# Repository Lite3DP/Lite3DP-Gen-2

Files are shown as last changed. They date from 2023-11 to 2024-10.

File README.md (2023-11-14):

# Lite3DP Gen 2

CAMP-8-pledge2a

Hi everyone! Thanks for stopping by here!

We are delighted to introduce the new Lite3DP Gen 2. We will be here expanding and improving the open source documentation, with a focus on the study, modification, improvement and repair of the kits and pre-assembled machines offered on [Crowd Supply](https://www.crowdsupply.com/lite3dp/lite3dp-gen-2).

Due to the need to introduce custom components and more complex manufacturing processes, we have moved slightly away from the strong DIY imprint of the S1 model, in which all the components are standard and the soldering with through-hole. However, for those enthusiasts who want to build an entirely Gen 2-style machine (OLED auxiliary display suggested), below we list non-standard components and possible adaptations/solutions.

1. SMD soldering.
Most electronic components are no longer through-hole and surface mount must be performed. It's not as simple as with a soldering iron, but you can order a stencil along with the PCBs, use solder paste and an electric oven or heat gun to achieve reflow. Please research this topic carefully.

2. Stepper motor.
We incorporate a custom stepper motor: Nema 8 with built-in T3.5 leadscrew, 128mm long. This is not a standard motor, but it is common to find a 100mm long leadscrew, which you can use only by giving up a few millimeters of build height.
   
3. LCD display.
We use a non-standard LCD display, with custom FPC cable and protective glass. You can get it as a spare part on [Crowd Supply](https://www.crowdsupply.com/lite3dp/lite3dp-gen-2).
   
4. Linear guide.
Like the stepper motor leadscrew, the 115mm length of the linear guide is not common, but you can also use 100mm length instead.
   
5. Aluminum light cone.
The original cone is made from aluminum, offering a large additional heat dissipation surface area. Use the plastic model with caution that the LCD display does not exceed 60°C. You can apply aluminum film inside and reduce the power of UV light.
    
6. Resin vat / build platform.
Resin vat can be made of plastic only in PLA and PP since other materials chemically react with resins. In the plastic alternative resin vat design, the Gerber of an aluminum PCB is included from which it can be cut out and obtain the vat frame and the surface of the build platform. This way it is not necessary to order metal cutting parts, and they can be ordered together with the PCBs.

Please visit our website [Lite3DP.com](https://www.lite3dp.com/) and we welcome inquiries at support@lite3dp.com. Thank you!

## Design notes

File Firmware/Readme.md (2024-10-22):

Please install ESP32 boards core **version 2.0.17** or earlier for Arduino IDE. (Newer 3.X.X versions have renamed some functions).

Attached "example.png" is an example section that, when copied to the root of the micro SD card, allows you to run the "Factory test".

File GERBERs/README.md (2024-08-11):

**Main board:**





**Aluminum base board:**



**OLED board:**



**4PDT switch board:**



**AUX CONN BOARD:**



**EXPANSION SHIELD (BETA):**



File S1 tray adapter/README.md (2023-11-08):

The S1 resin tray adapter can be printed on the S1 itself or on a filament 3D printer as well.
Please print two units, one for each side of the tray.

You will additionally need 4 M3x8 button head screws and 4 M3 nuts. (The magnets on the main board are not necessary. The resin tray attachment system is sliding, no longer magnetic).

Please note that the S1 build platform is perfectly compatible with the new Gen 2 Dev kit.



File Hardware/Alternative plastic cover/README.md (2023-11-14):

Plastic cover to be 3D printed.



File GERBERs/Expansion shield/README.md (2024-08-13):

**BETA version**

This is a 4 layer PCB, containing:

- 1 x Stepper motor driver (slow motion due to I2C conn.), with motor connector and microstep selector (1x3 dip switch).
- 2 x Servo outputs (+5V lvl).
- 2 x Endstops input (+5V lvl).
- 1 x +12V output (typ. a 12V fan).
- 1 x Buzzer.
- 5 x GPIO +3V3 lvl.
- 2 x GPIO +5V lvl.



You can use the following library for its control:

https://github.com/adafruit/Adafruit_AW9523?tab=readme-ov-file

To be plugged into the Gen 2 auxiliary connector.

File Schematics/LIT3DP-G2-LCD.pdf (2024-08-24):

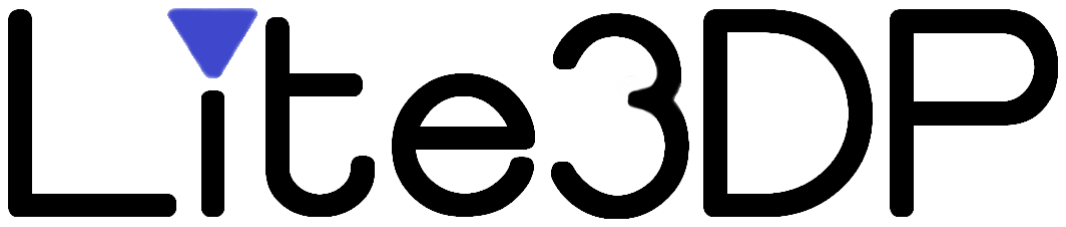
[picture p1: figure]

LITE3DP-G2-LCD | REV 1.0

# GEN 2

# SPECIFICATION FOR LCD MODULE

# LITE3DP-G2-LCD

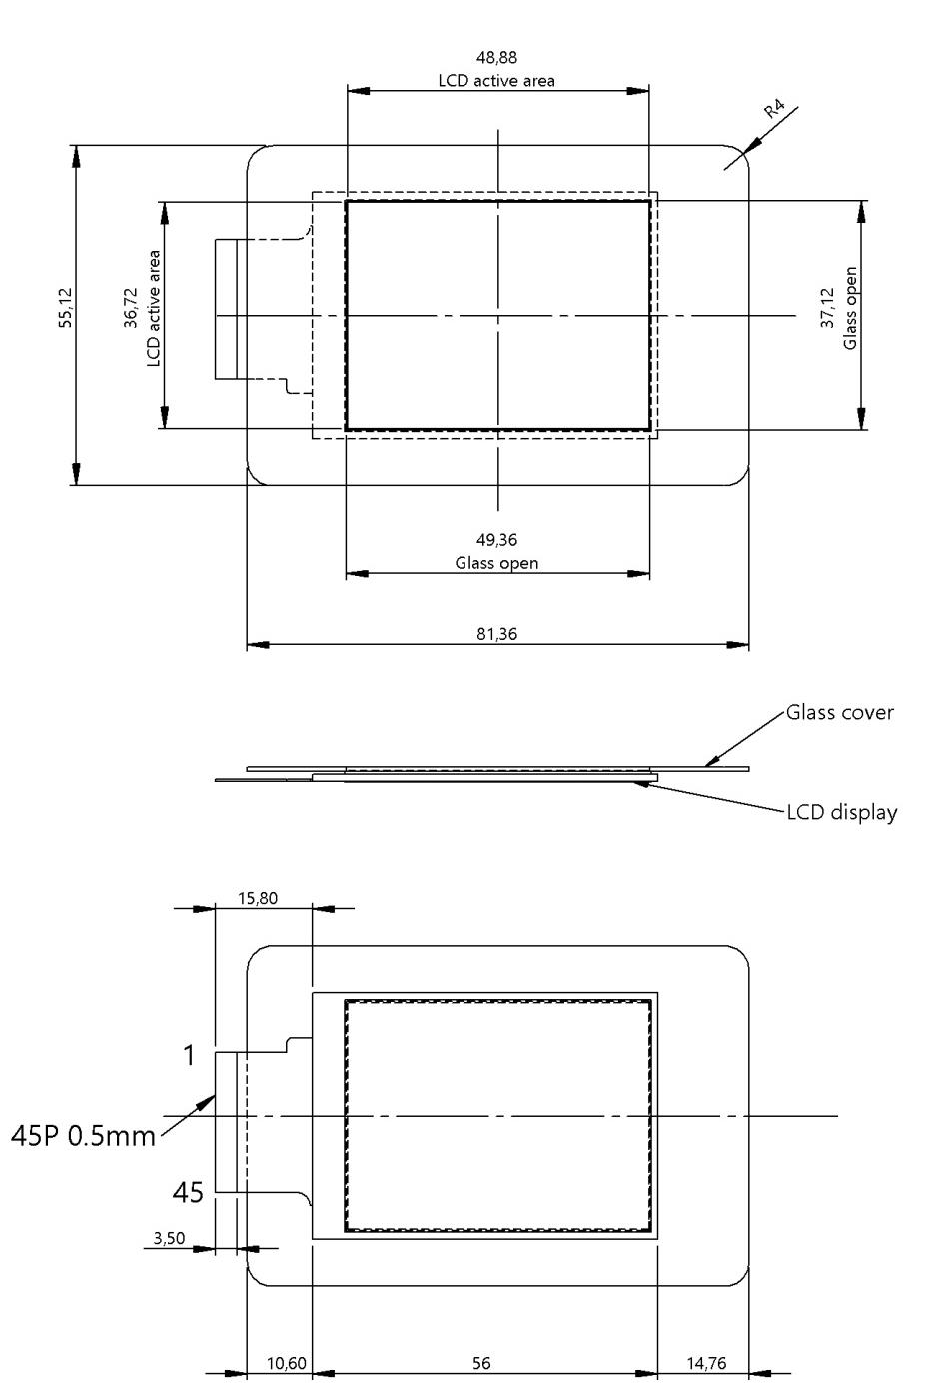
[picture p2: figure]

LITE3DP-G2-LCD | REV 1.0

PIN N°
1 | GND
2 | VCI
3 | IOVCC
4 | IM2
5 | IM1
6 | IM0
7 | RST
8 | CS
9 | DC
10 | WR(SPI SCL)
11 | RD
12 | VSYNC
13 | HSYNC
14 | ENABLE
15 | DOTCLK
16 | SDA
17 | DB0
18 | DB01
19 | DB02
20 | DB03
21 | DB04
22 | DB05
23 | DB06
24 | DB07
25 | DB08
26 | DB09
27 | DB10
28 | DB11
29 | DB12
30 | DB13
31 | DB14
32 | DB15
33 | DB16
34 | DB17
35 | SDO
36 | NC
37 | NC
38 | NC
39 | NC
40 | NC
41 | NC
42 | NC
43 | NC
44 | NC
45 | GND
DISPLAY TYPE | 2.4” – TFT LCD. 65K/262K COLORS
ACTIVE AREA | 36.72 x 48.88 mm
NUMBER OF PIXELS | 320(RGB) X 426
PIXEL PITCH | 0.11475 X 0.11475 mm
DISPLAY MODE | TRANSMISSIVE/NORMALLY BLACK
VIEWING DIRECTION | ALL
LCM DRIVER IC | ST7796S
LCM INTERFACE | SPI+RGB/MCU
VDD/VCI | 3.3V; IOVCC: 1.8-3.3V
OPERATING TEMPERATURE STORAGE TEMPERATURE | -20°C TO 70°C -30°C TO 80°C
ROHS COMPLIANT | YES

IM2 = IM1 = IM0 = 1: 4-WIRE 8 BIT DATA SERIAL INTERFACE (SDA, SCL, CS, RS).

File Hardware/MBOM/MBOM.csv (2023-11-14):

Nuts & screws | Qty
Aluminum spacers, length 35mm | 7
Nylon spacer, length 35mm | 1
M3x6 screw, allen button head | 10
M3x8 screw, allen button head | 24
M2x6 screw, allen cylindrical head | 8
M3x10 screw, allen countersunk head | 4
M3x10 hand knob screw | 1
M2x8 screw, allen cylindrical head | 3
M2 nuts | 4
M3 nuts | 4
Mechanical components
NEMA 8, leadscrew T3.5, length 118mm | 1
Linear guide rail MGN7, length 115 mm + MGN7C block | 1

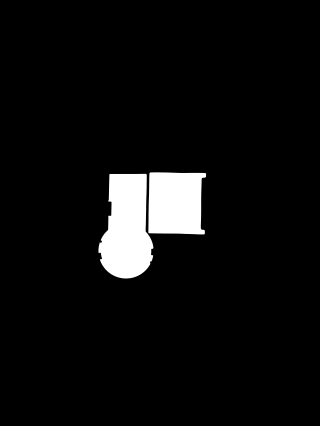
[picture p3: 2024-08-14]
Firmware/example.png

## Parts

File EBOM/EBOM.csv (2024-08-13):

 | MAIN BOARD
ID | Name | Designator | Footprint | Quantity | Manufacturer Part | Manufacturer | Supplier | Supplier Part
1 | 100nF | C2,C6,C8 | C0805 | 3 | GRM21BR71H104KA01L | MuRata | LCSC | C77082
2 | 10uF | C3 | C0805 | 1 | 0805X106K250NT | FH | LCSC | C40894
3 | 22uF | C7 | C0805 | 1 | CL21A226MAYNNNE | Samsung Electro-Mechanics | LCSC | C602037
4 | SS34_C8678 | D2 | DO-214AC_L4.3-W2.7-LS5.3-RD | 1 | SS34 | MDD | LCSC | C8678
5 | FH-00538 | H2 | HDR-SMD_12P-P2.54-V-F-R2-C6-S7.0-EH | 1 | FH-00538 | Liansheng(??) | LCSC | C2685123
6 | 150? | R3,R18 | R0805 | 2 | 0805W8J0151T5E | UniOhm | LCSC | C25283
7 | 10k? | R4,R5,R6,R7,R8,R9,R10,R11,R12,R19 | R0805 | 10 | RTT05103JTP | RALEC | LCSC | C103914
8 | 100k? | R13,R14,R15 | R0805 | 3 | RTT05104JTP | RALEC | LCSC | C103915
9 | 5.1k? | R16 | R0805 | 1 | 0805W8J0512T5E | UniOhm | LCSC | C26023
10 | ESP32-WROOM-32E(4MB) | U5 | WIFI-SMD_ESP32-WROOM-32E | 1 | ESP32-WROOM-32E(4MB) | Espressif Systems | LCSC | C701341
11 | DSHP03TS-S | SW1 | SW-SMD_DSHP03TS-S | 1 | DSHP03TS-S | XKB Enterprise | LCSC | C319051
12 | GT-TC029B-H025-L1N | BOOT,RST | SW-SMD_L3.9-W2.9-P4.15-LS5.0 | 2 | GT-TC029B-H025-L1N | G-Switch | LCSC | C843669
13 | 19-217/G7C-AN1P2/3T | LED1 | LED0603-R-RD | 1 | 19-217/G7C-AN1P2/3T | EVERLIGHT | LCSC | C72042
14 | PT4115 | U1 | SOT-89-5_L4.5-W2.5-P1.50-LS4.5-BR | 1 | PT4115 | UMW(???????) | LCSC | C347356
15 | LR1117DS33X | U2 | SOT-223_L6.3-W3.5-P2.30-LS7.0-BR-1 | 1 | LR1117DS33X | Leshan Radio | LCSC | C383259
16 | 100uF | C1 | SMD,D6.3xL7.7mm | 1 | RVT1H101M0607 | ROQANG(??) | LCSC | C3151829
17 | 10uF | C4,C5 | CAP-SMD_L3.5-W2.8-R-RD | 2 | TAJB106M025RNJ | AVX | LCSC | C8018
18 | TF-013 | CARD1 | TF-SMD_TF-013 | 1 | TF-013 | ???? | LCSC | C961683
19 | WAFER-254L-4P | CN2,CN4 | CONN-SMD_WAFER-254L-4P | 2 | WAFER-254L-4P | XUNPU(??) | LCSC | C2856686
20 | SS14_C211769 | D1 | SMA_L4.4-W2.8-LS5.4-RD | 1 | SS14 | Yangzhou Yangjie Elec Tech | LCSC | C211769
21 | THD0515-45CL-SN | FPC1 | FFC-SMD_45P-P0.50_THD0515-45CL-SN | 1 | THD0515-45CL-SN | THD | LCSC | C283158
22 | 47uH | L1 | IND-SMD_L5.0-W5.0_NR5040T | 1 | SNR5040TYD470M | SOREDE(???) | LCSC | C2827400
23 | D882 | Q1 | SOT-89-3_L4.5-W2.5-P1.50-LS4.2-BR | 1 | D882 | Hottech | LCSC | C181187
24 | 160m? | R1 | R2010 (1%) | 1 | RTT20R160FTE | RALEC | LCSC | C333477
25 | 180m? | R2 | R2010 (1%) | 1 | FRL2010FR180TS | FOJAN | LCSC | C2934352
26 | 30? | R17 | R2010 | 1 | RTT2030R0FTE | RALEC | LCSC | C458673
27 | SMD1206B075TF/16 | U8 | R1206 | 1 | SMD1206B075TF/16 | Brightking Elec (TAIWAN) | LCSC | C269118
28 | GT-TC041B-H036-L1N COPY | SP | G-SWITCH GT-TC041B-H036-L1N | 1 | GT-TC041B-H036-L1N | G-Switch(??) | LCSC | C2686893
29 | 2171-104MS0CUNR1 | U3 | CONN-SMD_2171-104MS0CUNR1 | 1 | 2171-104MS0CUNR1 | Wcon(????) | LCSC | C920937
30 | DC-050-20A | DC1 | DC-IN-SMD_DC-050-20A | 1 | DC-050-20A | ???? | LCSC | C707276
31 | F0502-B-12-20T-R | FPC2 | FPC-SMD_F0502-B-12-20T-R | 1 | F0502-B-12-20T-R | XFCN | LCSC | C705230
32 | DY-ITR8402 | U6 | OPTO-TH_DY-ITR8402 | 1 | DY-ITR8402 | TONYU | LCSC | C390039
33 | SS-12D10L4 | SW2 | SW-TH_SS-12D10L3 | 1 | SS-12D10L4 | XKB Connectivity | LCSC | C843364
34 | 2171-104MS0CUNR1 | U10, U11 | CONN-SMD_2171-108MS0CUNR1 | 2 | 2171-108MS0CUNR1 | Wcon(????)
35 | Custom LCD | - | LCD-display | 1 | LITE3DP-G2-LCD | LITE3DP |  |  | https://www.crowdsupply.com/lite3dp/lite3dp-gen-2
 | BASE BOARD
ID | Name | Designator | Footprint | Quantity | Manufacturer Part | Manufacturer | Supplier | Supplier Part
1 | LED-SMD_L3.5-W2.8-RD_1.25T-2PWT | U1,U2 | LED-SMD_L3.5-W2.8-RD_1.25T-2PWT | 2 | XL-2835UWC-02 | XINGLIGHT(???) | LCSC | C2843876
2 | WAFER-254L-4P | CN1 | CONN-SMD_WAFER-254L-4P | 1 | WAFER-254L-4P | XUNPU(??) | LCSC | C2856686
2 | LED 10W UV 405 nm | U3 | 6565 | 1 |  | YM | N/A on LCSC |  | https://aliexpress.com/item/1005004873818397.html
 |  |  |  |  |  |  |  |  | REMOVE QUARTZ LENS
 | OLED BOARD
ID | Name | Designator | Footprint | Quantity | Manufacturer Part | Manufacturer | Supplier | Supplier Part
1 | 10uF | C1,C3,C4,C5 | C0805 | 4 | 0805X106K250NT | FH | LCSC | C40894
2 | 100nF | C2 | C0805 | 1 | GRM21BR71H104KA01L | MuRata | LCSC | C77082
3 | 1125-1104G0Z135CR01 | CN1 | CONN-SMD_1125-1104G0Z135CR01 | 1 | 1125-1104G0Z135CR01 | Wcon(????) | LCSC | C721862
4 | LMBR120FT1G | D2 | SOD-123_L2.8-W1.8-LS3.7-RD | 1 | LMBR120FT1G | LRC(?????) | LCSC | C81143
5 | 10uH | L1 | L0805 | 1 | MGFL2012F100MT-LF | microgate | LCSC | C281113
6 | 12k? | R1,R3,R4 | R0805 | 3 | 0805W8J0123T5E | UniOhm | LCSC | C25616
7 | 100k? | R2 | R0805 | 1 | RTT05104JTP | RALEC | LCSC | C103915
8 | 680k? | R5 | R0805 | 1 | 0805W8J0684T5E | UniOhm | LCSC | C25640
9 | 2.2k? | R6,R7 | R0805 | 2 | CR0805J80222G | LIZ | LCSC | C101970
10 | AP3012KTR-G1 | U1 | SOT-23-5_L2.9-W1.6-P0.95-LS2.8-BL | 1 | AP3012KTR-G1 | DIODES(??) | LCSC | C102618
11 | APX803S-26SA-7 | U2 | SOT-23-3_L2.9-W1.6-P1.90-LS2.8-BR | 1 | APX803S-26SA-7 | DIODES(??) | LCSC | C526393
12 | OLED DISPLAY | ER-OLED0.96-7 | 13 pins | 1 | ER-OLED0.96-7 | EastRising | EastRising | ER-OLED0.96-7 | https://www.buydisplay.com/white-0-96-inch-64x128-oled-display-screen-sh1107-spi-i2c-interface
 | 4PDT SWITCH BOARD
ID | Name | Designator | Footprint | Quantity | Manufacturer Part | Manufacturer | Supplier | Supplier Part
1 |  | IN1, IN2, OUT1, OUT2 | Male Header, 4 Pins x 1 Row, Straight, P=2.54 mm | 4 | 210-91-04GB01 | PINREX | LCSC | C390680
2 | 4PDT SWITCH |  |  | 1 | T-80 |  |  |  | https://aliexpress.com/i/1005004254583326.html
 |  |  |  |  |  |  |  |  | ON OFF ON
 | AUX CONN BOARD
ID | Name | Designator | Footprint | Quantity | Manufacturer Part | Manufacturer | Supplier | Supplier Part
1 | X6511FRS-05-C85D30 | H1 | HDR-SMD_5P-P2.54-H-F_X6511FRS-19-C85D30 | 1 | X6511FRS-05-C85D30 | XKB Connectivity(????) | LCSC | C5142238
2 | PZ254V-12-12P | H2 | HDR-TH_12P-P2.54-V-M-R2-C6-S2.54 | 1 | PZ254V-12-12P | XFCN(??) | LCSC | C492423
3 | PM254V-12-12-H85 | H3 | HDR-TH_12P-P2.54-V-F-R2-C6-S2.54 | 1 | PM254V-12-12-H85 | XFCN(??) | LCSC | C541855
 | EXPANSION SHIELD
ID | Name | Designator | Footprint | Quantity | Manufacturer Part | Manufacturer | Supplier | Supplier Part
1 | Header-Female-2.54_1x8 | EN,VMOT | HDR-TH_8P-P2.54-V-F-1 | 2 | 2.54-1*8P??? | BOOMELE(????) | LCSC | C27438
2 | PZ254V-11-04P_C2691448 | MOT | HDR-TH_4P-P2.54-V-M | 1 | PZ254V-11-04P | XFCN(??) | LCSC | C2691448
3 | PZ254V-11-02P | H4,H2,FAN | HDR-TH_2P-P2.54-V-M | 3 | PZ254V-11-02P | XFCN(??) | LCSC | C492401
4 | TXS0108EPWR | U2 | TSSOP-20_L6.5-W4.4-P0.65-LS6.4-BL | 1 | TXS0108EPWR | TI(????) | LCSC | C17206
5 | 5.1K | R2,R5 | R0603 | 2 | RC0603JR-075K1L | YAGEO(??) | LCSC | C14677
6 | 10k? | R4,R3,R8,R6,R7 | R0603 | 5 | 0603WAJ0103T5E | UNI-ROYAL(??) | LCSC | C15401
7 | D882 | Q2,Q1 | SOT-89-3_L4.5-W2.5-P1.50-LS4.2-BR | 2 | D882 | Hottech | LCSC | C181187
8 | AMS1117-5.0_C347223 | U3 | SOT-223_L6.7-W3.5-P2.30-BR | 1 | AMS1117-5.0 | UMW(???????) | LCSC | C347223
9 | AW9523BTQR | U1 | VFQFPN-24_L4.0-W4.0-P0.50-BL-EP2.8 | 1 | AW9523BTQR | AWINIC(??) | LCSC | C148077
10 | SS34_C8678 | D2 | DO-214AC_L4.3-W2.7-LS5.3-RD | 1 | SS34 | MDD | LCSC | C8678
11 | 10uF | C5,C4 | CAP-SMD_L3.5-W2.8-R-RD | 2 | TAJB106M025RNJ | AVX | LCSC | C8018
12 | 100k? | R1 | R0603 | 1 | 0603WAJ0104T5E | UNI-ROYAL(??) | LCSC | C15458
13 | Header-Male-2.54_1x3 | E1,E2,S1,S2 | HDR-TH_3P-P2.54-V-M-1 | 4 | 2.54-1*3P? | BOOMELE(????) | LCSC | C49257
14 | MLT-5020 | BUZZ1 | BUZ-SMD_L5.0-W5.5-P4.60 | 1 | MLT-5020 | ?? | LCSC | C94598
15 | PZ254-1-13-Z-8.5 | H1 | HDR-TH_13P-P2.54-V-M | 1 | PZ254-1-13-Z-8.5 | HCTL(????) | LCSC | C2894936
16 | DSHP03TS-S | SW1 | SW-SMD_DSHP03TS-S | 1 | DSHP03TS-S | XKB Enterprise | LCSC | C319051
17 | 100uF | C1 | SMD,D6.3xL7.7mm | 1 | RVT1H101M0607 | ROQANG(??) | LCSC | C3151829
18 | 100nF | C2,C3 | C0603 | 2 | 0603B104K500NT | FH(??) | LCSC | C30926
19 | PZ254V-12-12P | H3 | HDR-TH_12P-P2.54-V-M-R2-C6-S2.54 | 1 | PZ254V-12-12P | XFCN(??) | LCSC | C492423

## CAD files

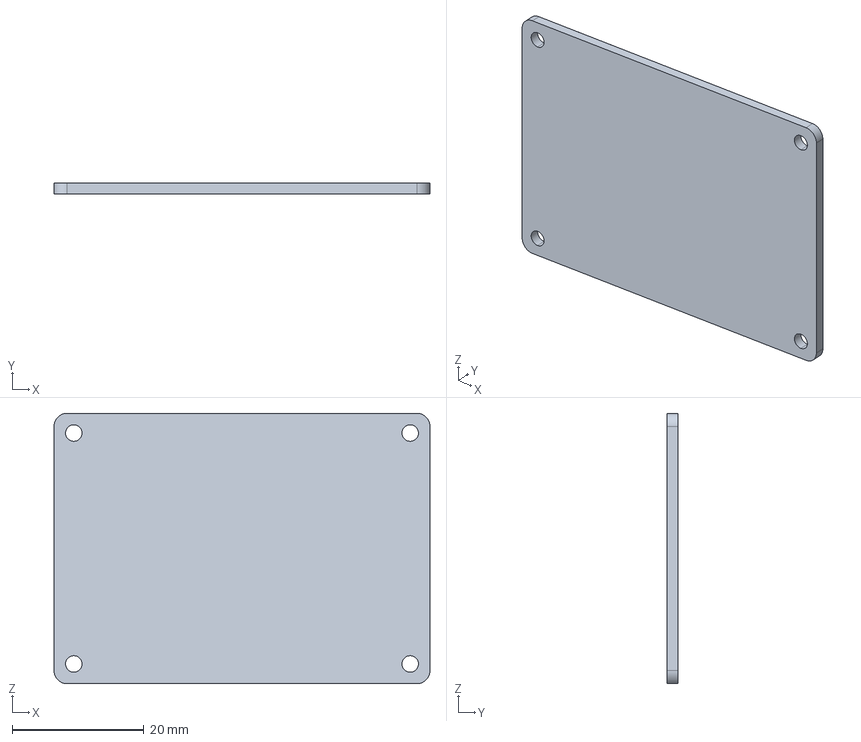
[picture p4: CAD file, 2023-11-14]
Alternative resin vat and build platform/Platform aluminum surface.STEP
57.0 x 1.60 x 41.0 mm

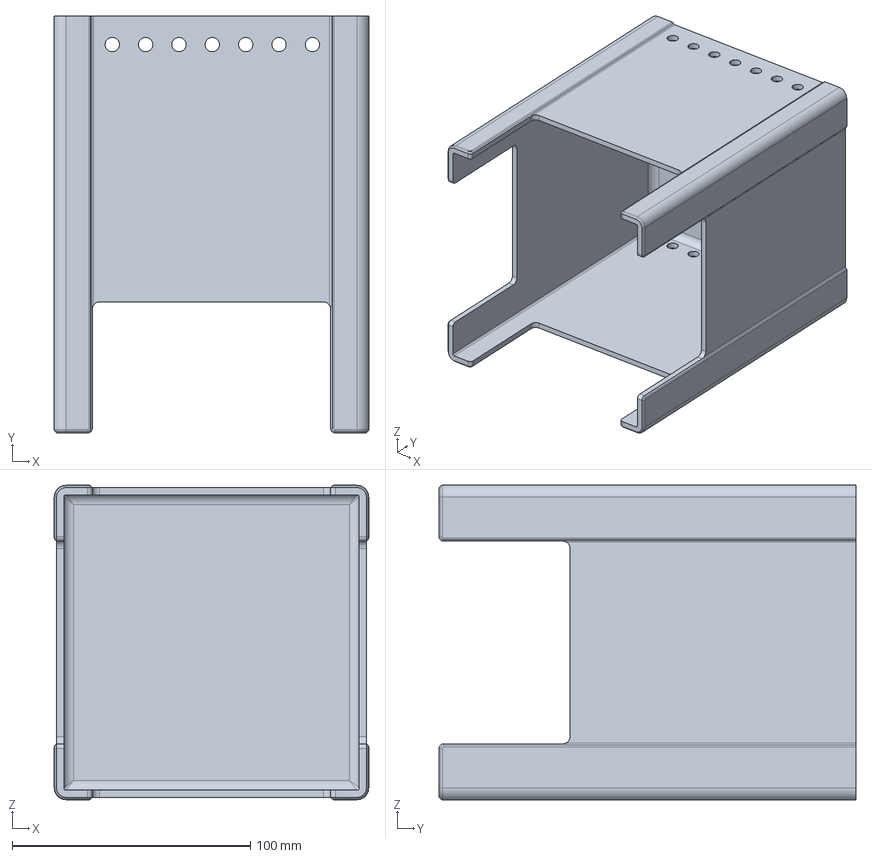
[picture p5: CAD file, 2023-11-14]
Hardware/Alternative plastic cover/Alternative cover.STEP
132.0 x 175.0 x 132.0 mm

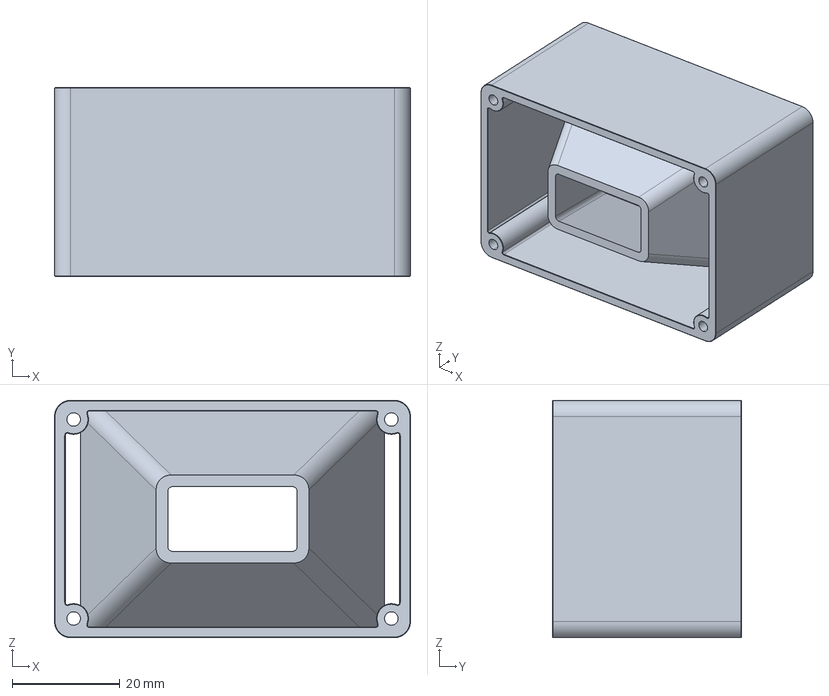
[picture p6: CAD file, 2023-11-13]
Hardware/Plastic parts/Cone.STEP
66.0 x 35.0 x 44.0 mm

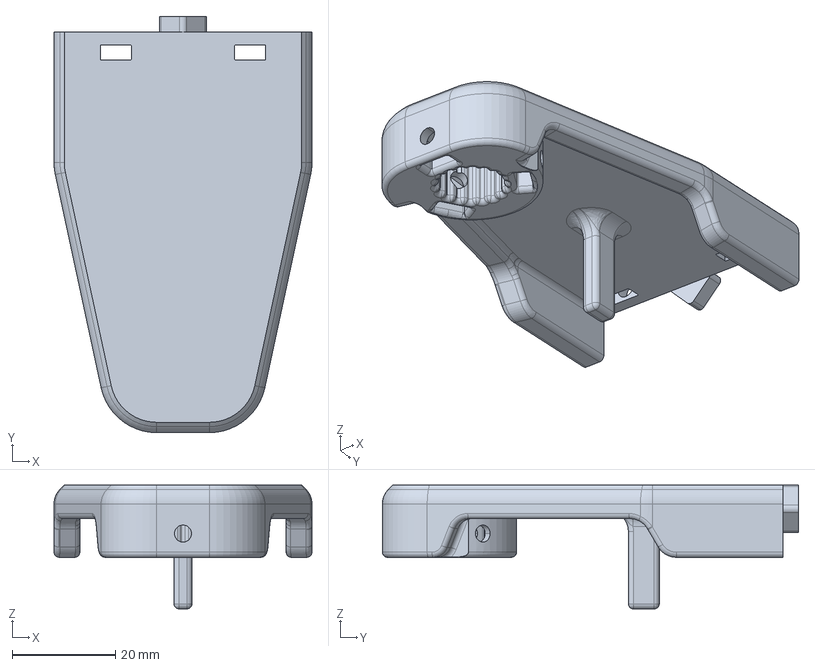
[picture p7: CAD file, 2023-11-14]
Platform carriage for FDM printers/Carriage part.STEP
50.0 x 80.7 x 24.0 mm

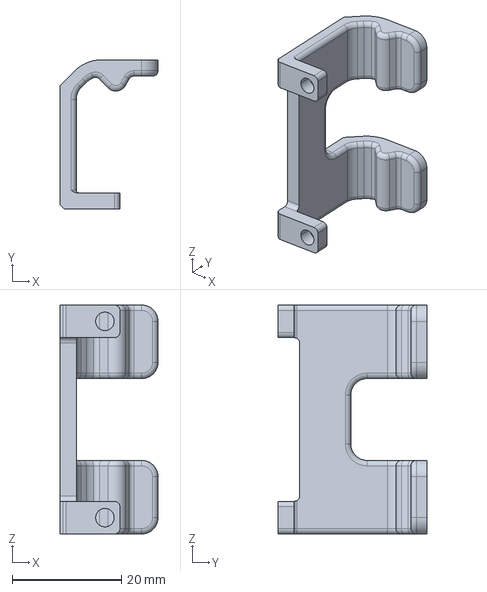
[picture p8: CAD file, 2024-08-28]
S1 tray adapter/S1 tray adapter.STEP
18.0 x 27.4 x 42.0 mm

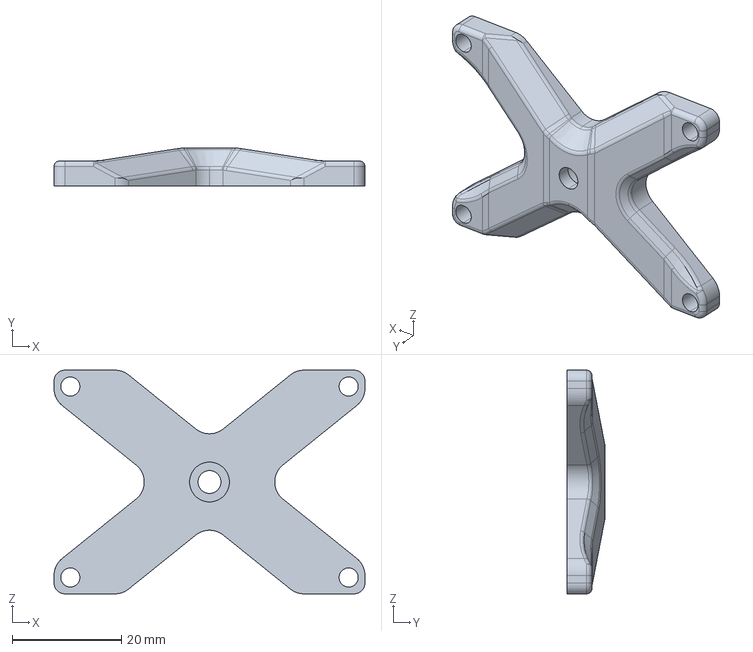
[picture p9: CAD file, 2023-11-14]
Alternative resin vat and build platform/Platform body.STEP
57.0 x 7.00 x 41.0 mm

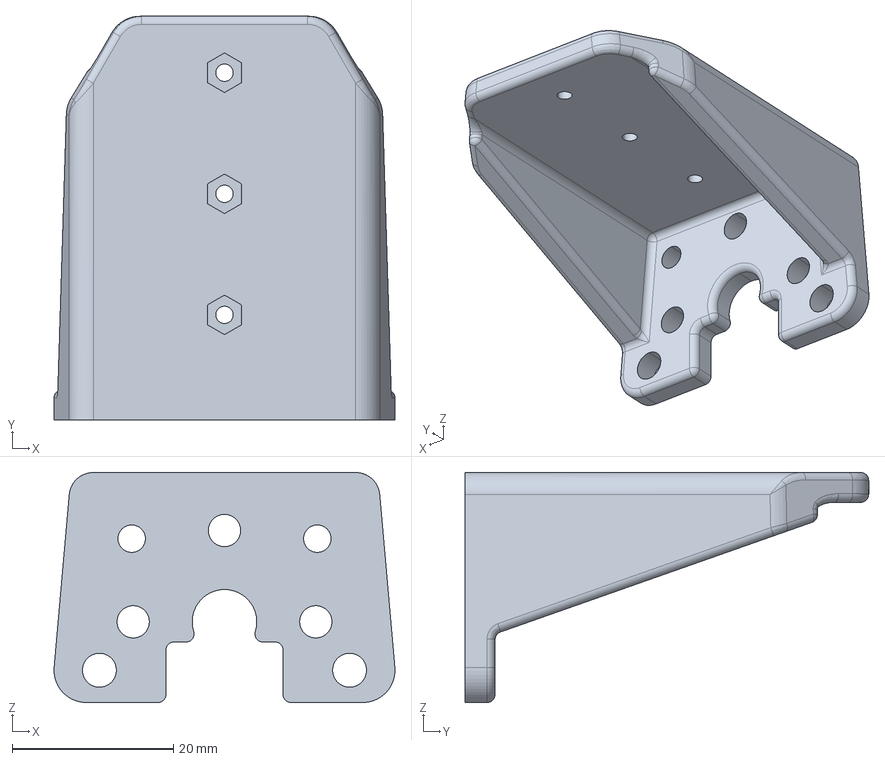
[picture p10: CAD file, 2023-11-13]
Hardware/Plastic parts/Support.STEP
42.3 x 50.0 x 28.5 mm

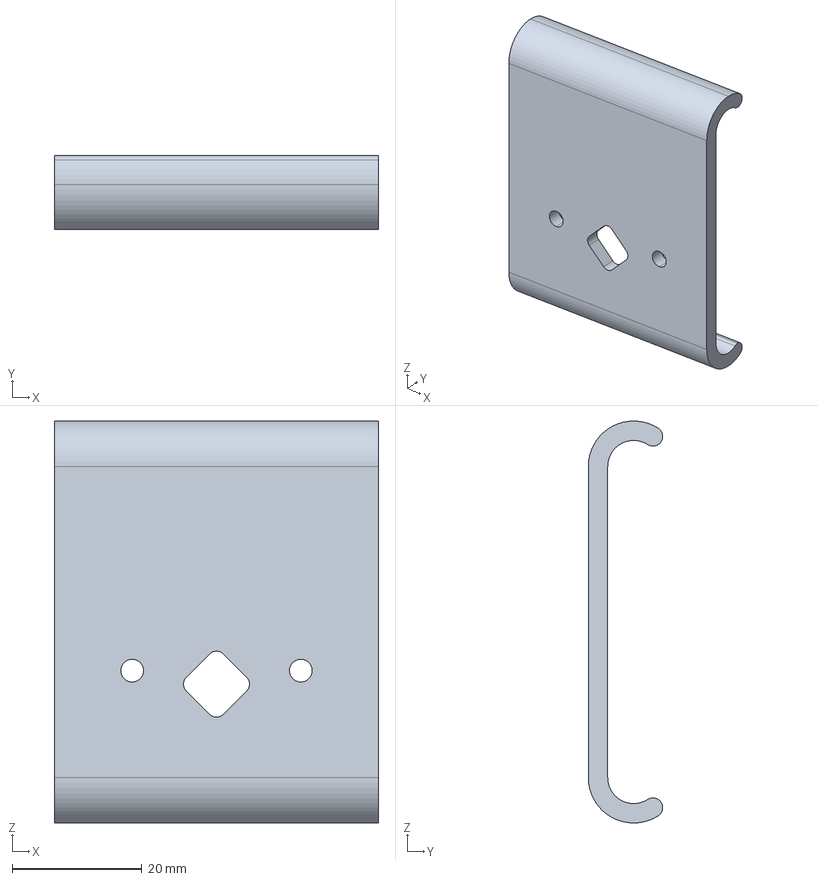
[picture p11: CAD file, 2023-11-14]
Platform carriage for FDM printers/Holding part.STEP
50.0 x 11.5 x 62.0 mm

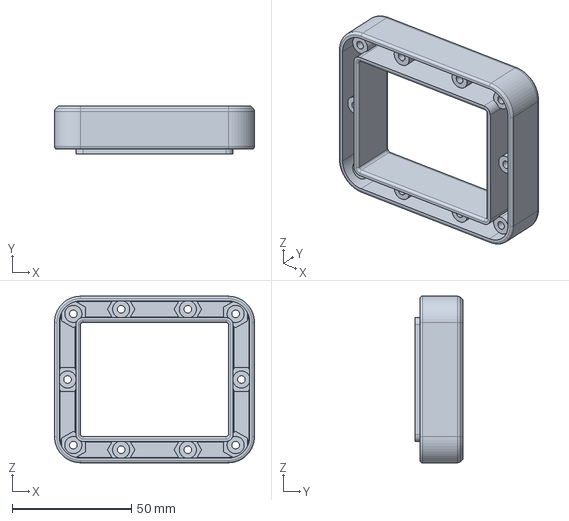
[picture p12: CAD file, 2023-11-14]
Alternative resin vat and build platform/Plastic vat.STEP
84.0 x 20.0 x 70.0 mm

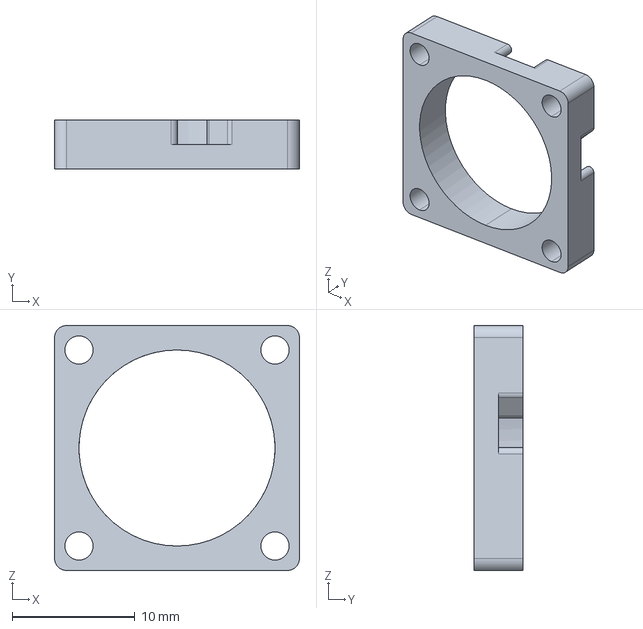
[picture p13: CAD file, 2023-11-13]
Hardware/Plastic parts/Nema 8 spacer.STEP
20.0 x 4.00 x 20.0 mm

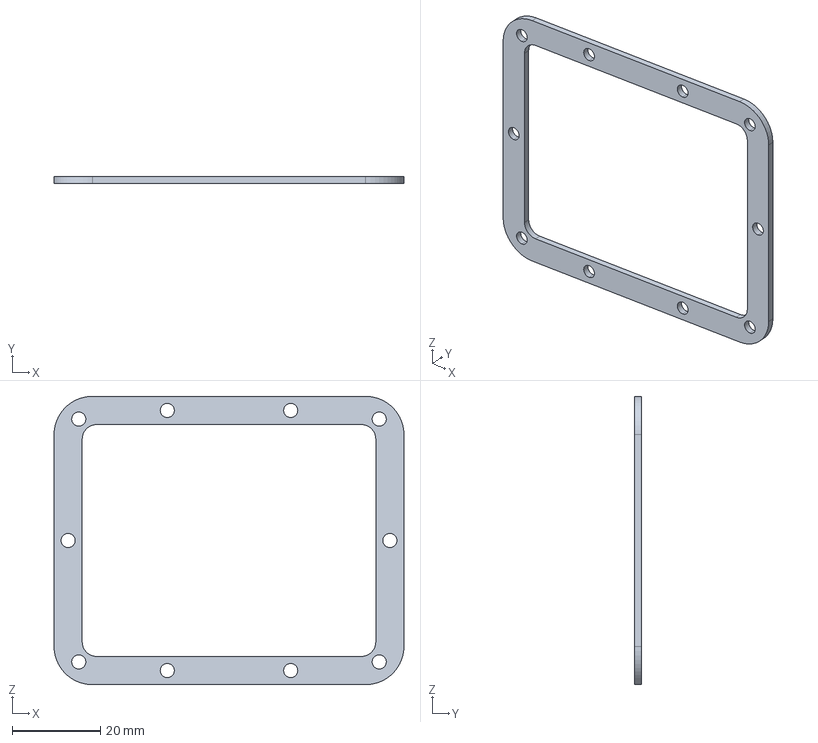
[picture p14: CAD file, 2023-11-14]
Alternative resin vat and build platform/vat frame.STEP
79.4 x 1.60 x 65.4 mm

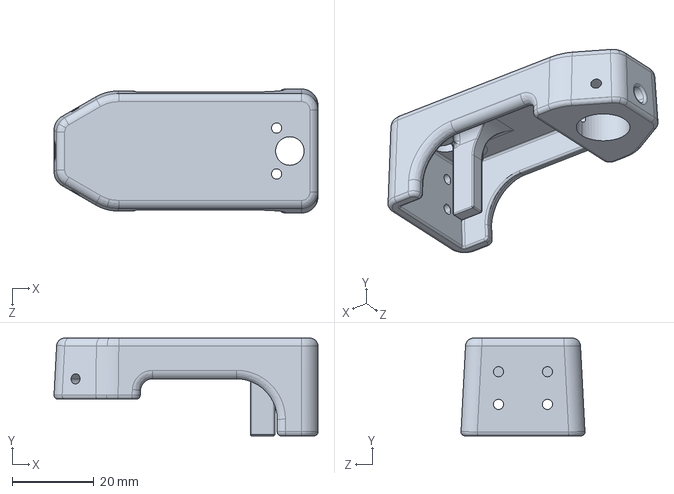
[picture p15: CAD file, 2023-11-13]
Hardware/Plastic parts/Carriage.STEP
64.7 x 24.0 x 30.4 mm

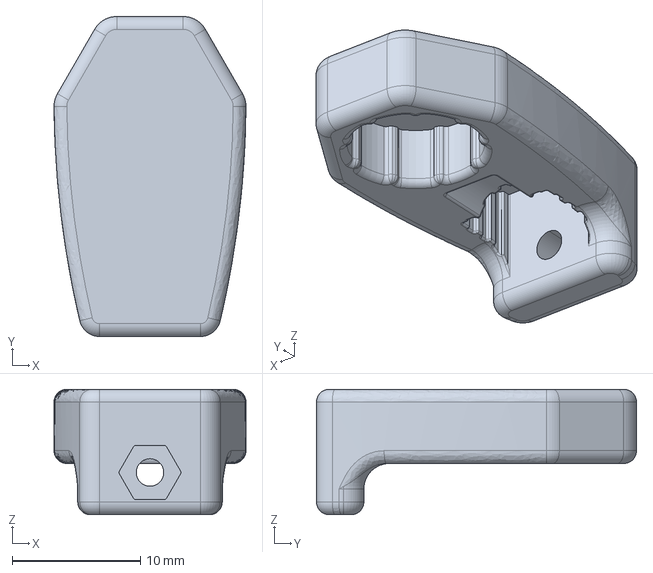
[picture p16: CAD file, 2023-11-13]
Hardware/Plastic parts/Bearing housing.STEP
15.0 x 25.0 x 9.80 mm

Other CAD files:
Alternative resin vat and build platform/Plastic vat.STL
Alternative resin vat and build platform/Platform body.STL
Hardware/Alternative plastic cover/Alternative cover.STL
Hardware/Plastic parts/Cone.STL
Hardware/Plastic parts/Nema 8 spacer.STL
Hardware/Plastic parts/Support.STL
Platform carriage for FDM printers/Carriage part.STL
Platform carriage for FDM printers/Holding part.STL
S1 tray adapter/S1 tray adapter.STL

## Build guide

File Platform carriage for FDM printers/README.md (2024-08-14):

Reference model to be adapted to your filament 3D printer. In addition to the printed parts, you will also need:
1) M3x8 screws, Qty. 2
2) M3x10 screws, Qty. 3 (One of them may have a hand knob)
3) M3 nuts, Qty. 5
4) Concave magnet. Reference: https://www.aliexpress.com/item/2251832403850307.html





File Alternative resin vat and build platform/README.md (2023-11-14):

Resin vat and build platform to be built with printed parts (PLA or PP) and a set of aluminum PCBs. Use with S1 tray adapter set.

You will need:
1) M3x16 screw, allen cylindrical head, Qty. 10 (resin vat)
2) M3 nuts, Qty. 10 (resin vat)
4) M3x6 screw, allen button head, Qty. 4 (build platform)
5) M4x16 screw, allen cylindrical head, Qty. 1 (build platform)
6) M4 nuts, Qty. 2 (build platform)
7) 10mm steel ball with M4 hole, Reference: https://www.aliexpress.com/item/2251832403850307.html







The Gerber file must be ordered as an aluminum PCB. Separate the two pieces with a file or saw: vat frame and platform surface.



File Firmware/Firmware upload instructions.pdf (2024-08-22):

## Firmware upload to Lite3DP Gen 2 mainboard

1. Check that the computer to be used does not already have a library with one of the following names:

"SdFat"

"Adafruit_GFX"

"Adafruit_BusIO"

“Adafruit_SH110X”

“PNGdec”

“TFT-eSPI”

“XPT2046_Touchscreen”

In case you have a library of the same name, please delete it (or temporarily move it to another location), since another version of the libraries will cause a malfunction.

2. Add the 7 attached libraries, one by one, in the Arduino IDE:

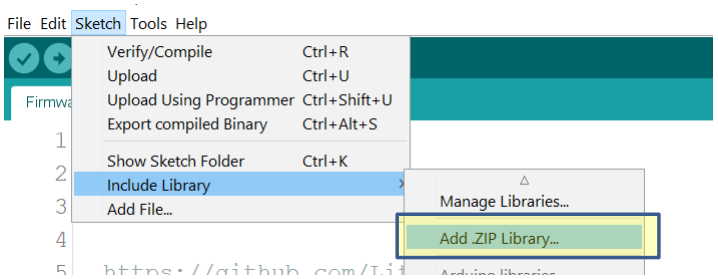
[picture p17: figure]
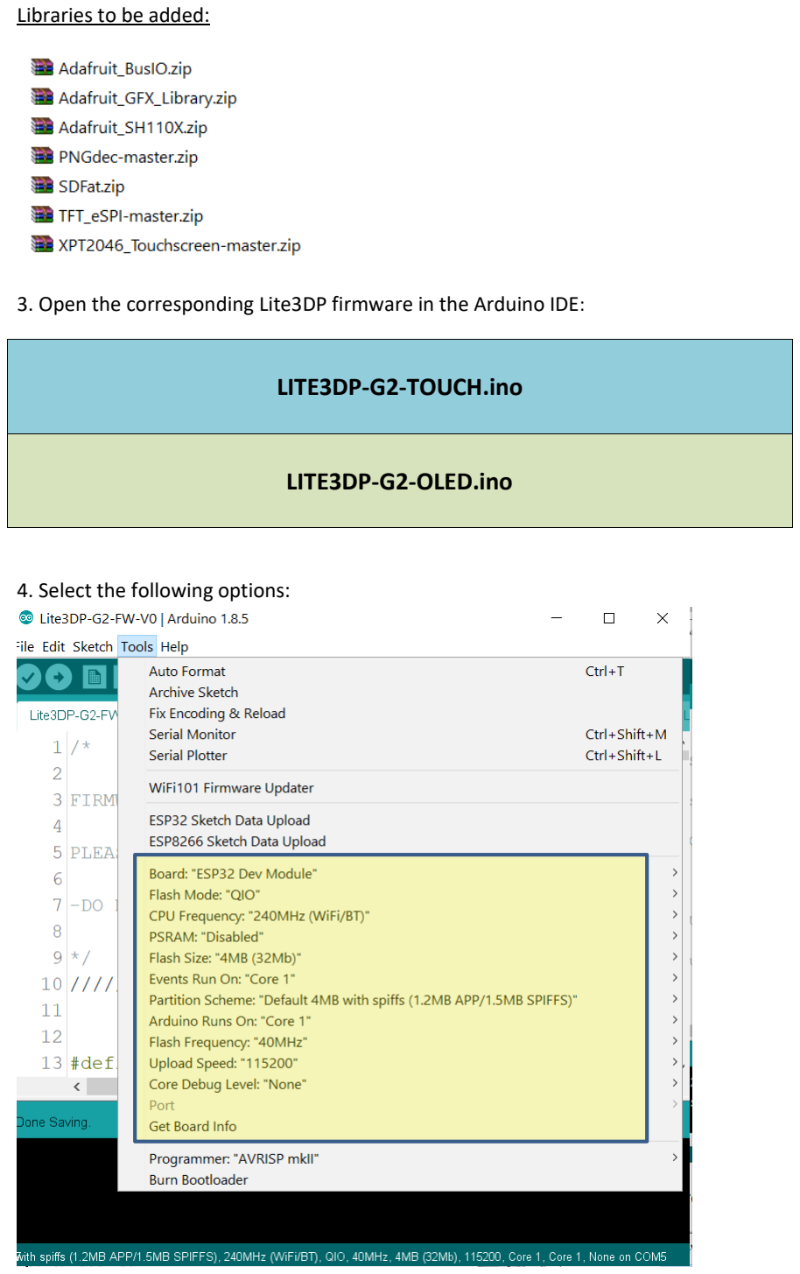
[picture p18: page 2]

Libraries to be added:

3. Open the corresponding Lite3DP firmware in the Arduino IDE:

LITE3DP-G2-TOUCH.ino

LITE3DP-G2-OLED.ino

4. Select the following options:

5. Hit verify/compile and you should get:

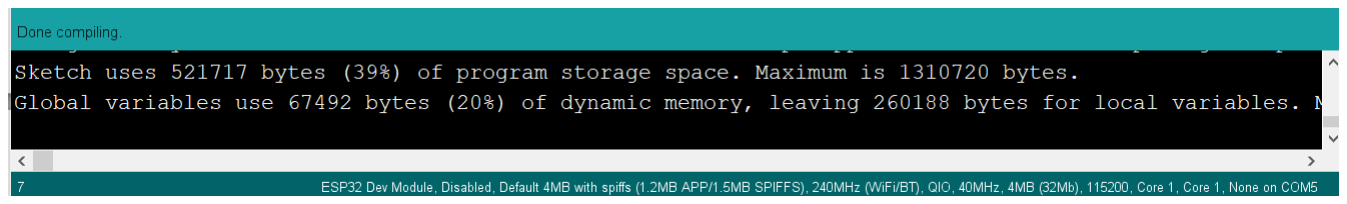
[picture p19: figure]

6. Connect the CP2102 board to the auxiliary connector and then the USB-C cable to computer.

CAUTION: Improper connection of the CP2102 board to the mainboard may cause permanent damage.

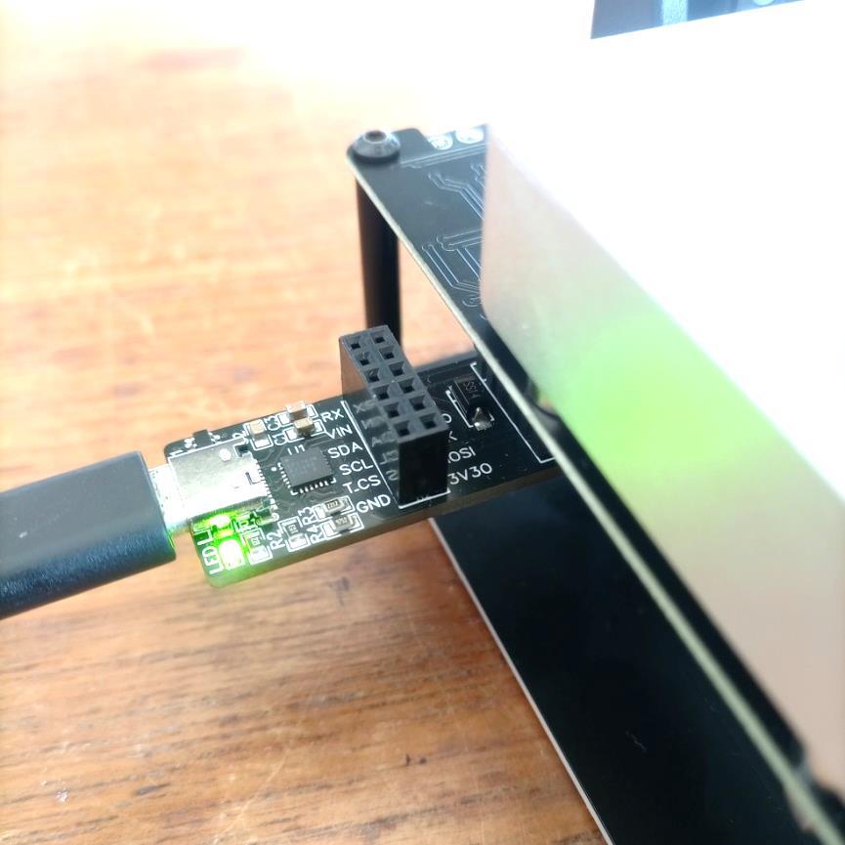
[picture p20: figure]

7. Before upload the firmware, press BOOT, and without releasing it, press RST. Let go of both buttons and the ESP32 will enter upload mode.

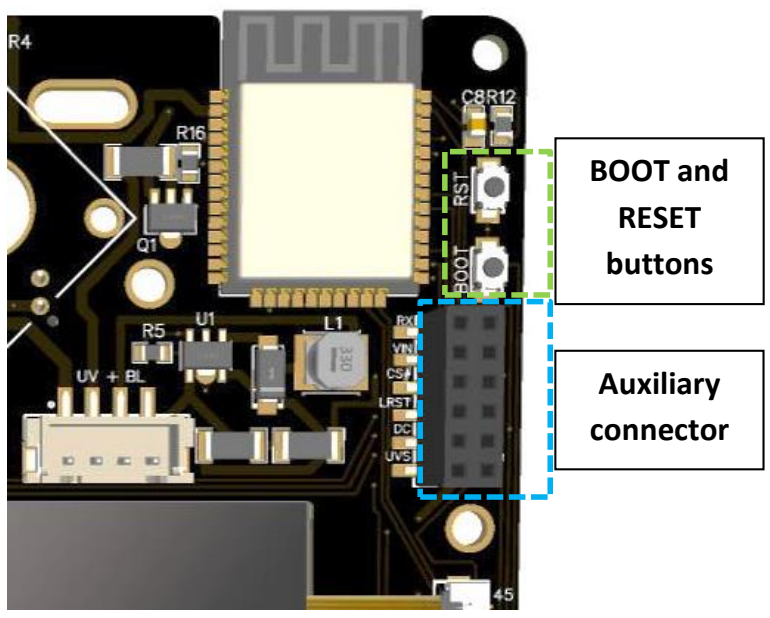
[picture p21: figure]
BOOT and RESET buttons; Auxiliary connector

8. Select the correct COM port.
9. Hit Upload until the upload is complete.

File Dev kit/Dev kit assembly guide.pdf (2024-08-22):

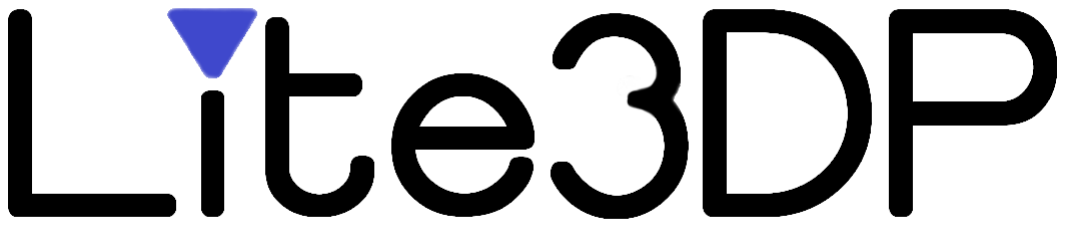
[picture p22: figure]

# Gen 2 dev. kit assembly guide

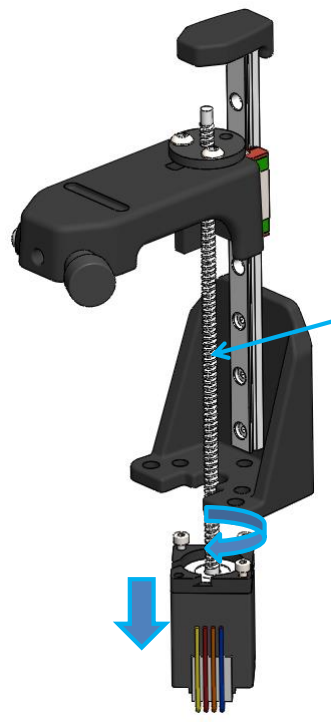
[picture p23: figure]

REMOVE THE STEPPER
MOTOR FROM THE PRE-ASSEMBLY

Manually turn the threaded rod of the motor until it
separates downwards

Threaded rod

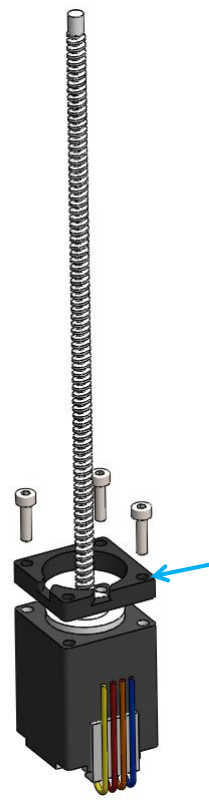
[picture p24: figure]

UNSCREW 3 SCREWS
(M2 X 8) FROM THE
STEPPER MOTOR

Spacer

UNSCREW THE 4 SCREWS IN THE CORNERS OF THE BASE

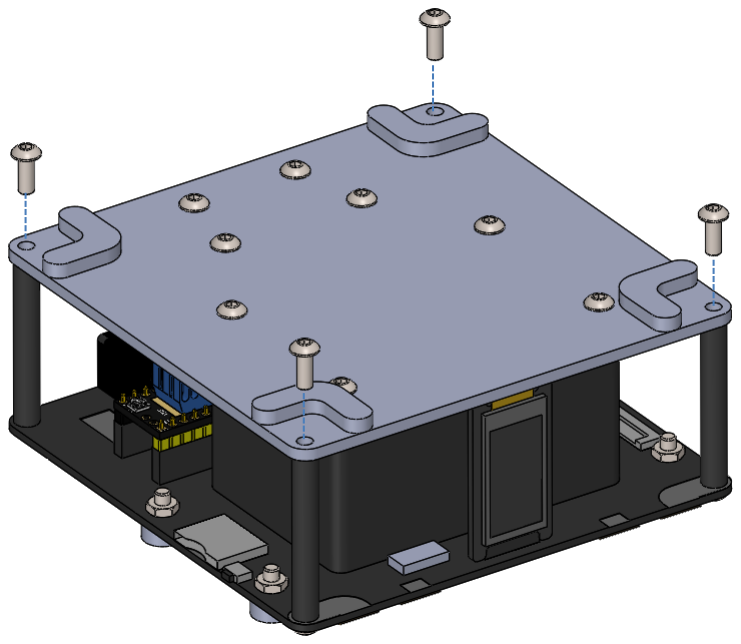
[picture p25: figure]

UNSCREW THE FOLLOWING

### 4 SCREWS

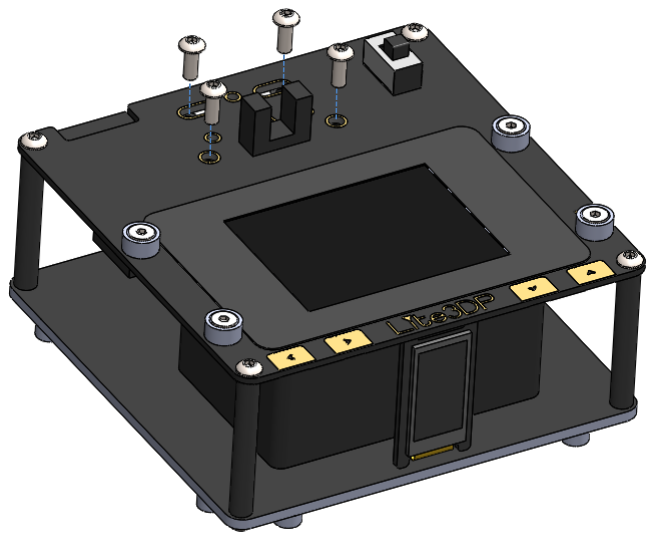
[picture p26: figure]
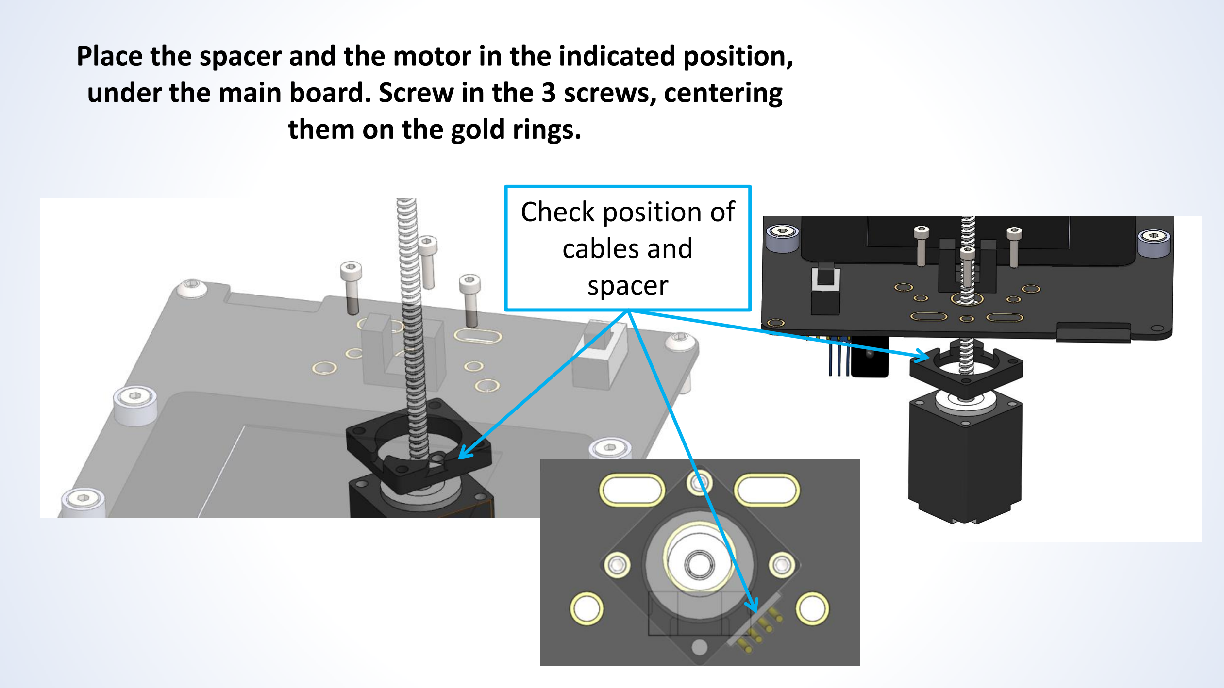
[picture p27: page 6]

Place the spacer and the motor in the indicated position, under the main board. Screw in the 3 screws, centering them on the gold rings.

Check position of
cables and
spacer

CONNECT THE STEPPER MOTOR CABLE

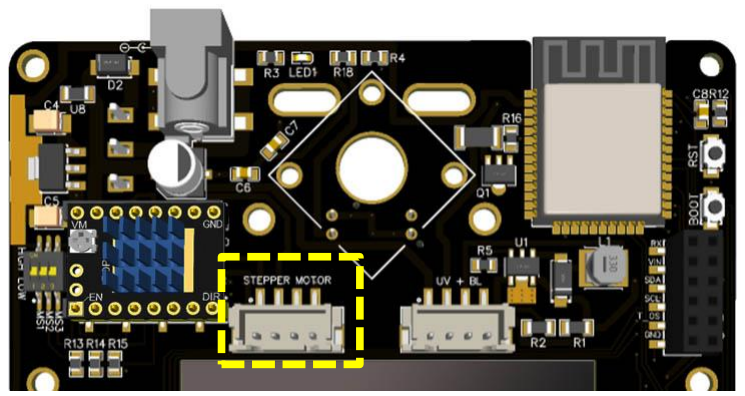
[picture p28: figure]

CONNECT THE BASE-MAIN BOARD CABLE

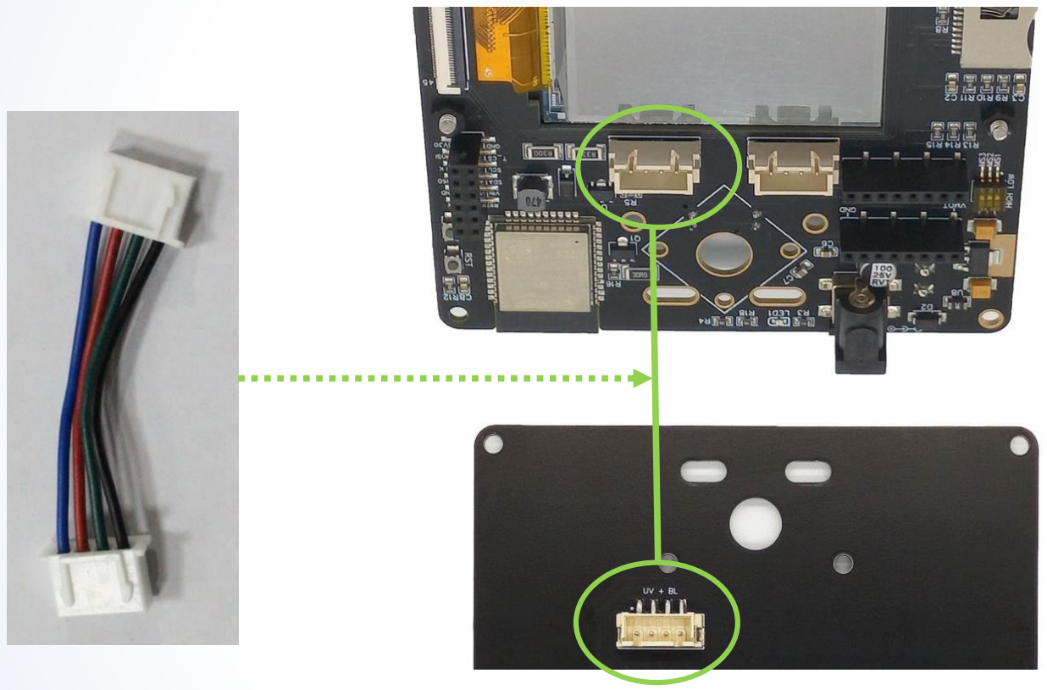
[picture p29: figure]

REASSEMBLE THE BASE WITH THE 4 CORNER SCREWS

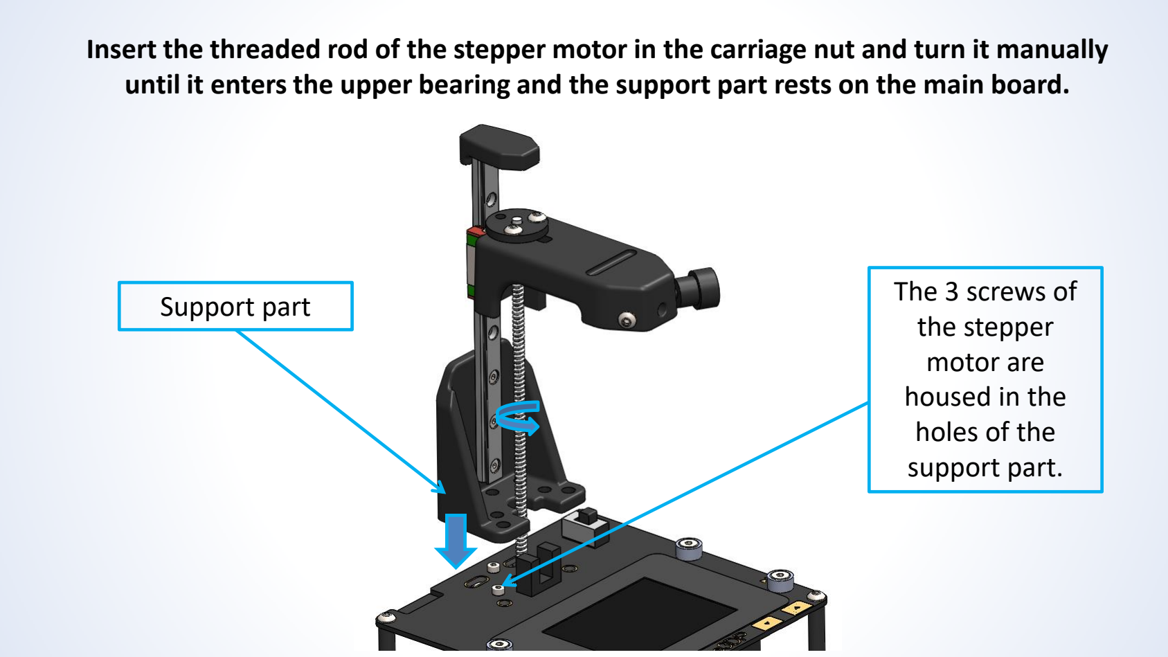
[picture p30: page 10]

Insert the threaded rod of the stepper motor in the carriage nut and turn it manually until it enters the upper bearing and the support part rests on the main board.

Support part | The 3 screws of the stepper motor are housed in the holes of the support part.

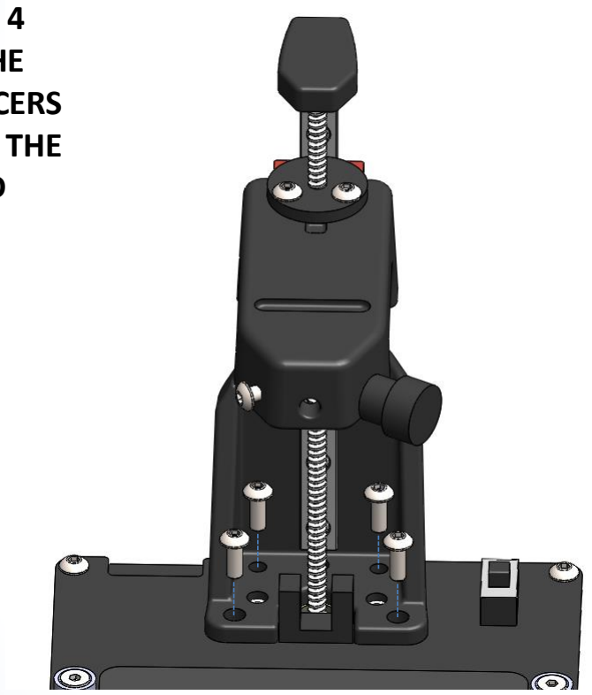
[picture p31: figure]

SCREW IN THE 4
SCREWS TO THE
ALUMINUM SPACERS
LOCATED UNDER THE
MAIN BOARD

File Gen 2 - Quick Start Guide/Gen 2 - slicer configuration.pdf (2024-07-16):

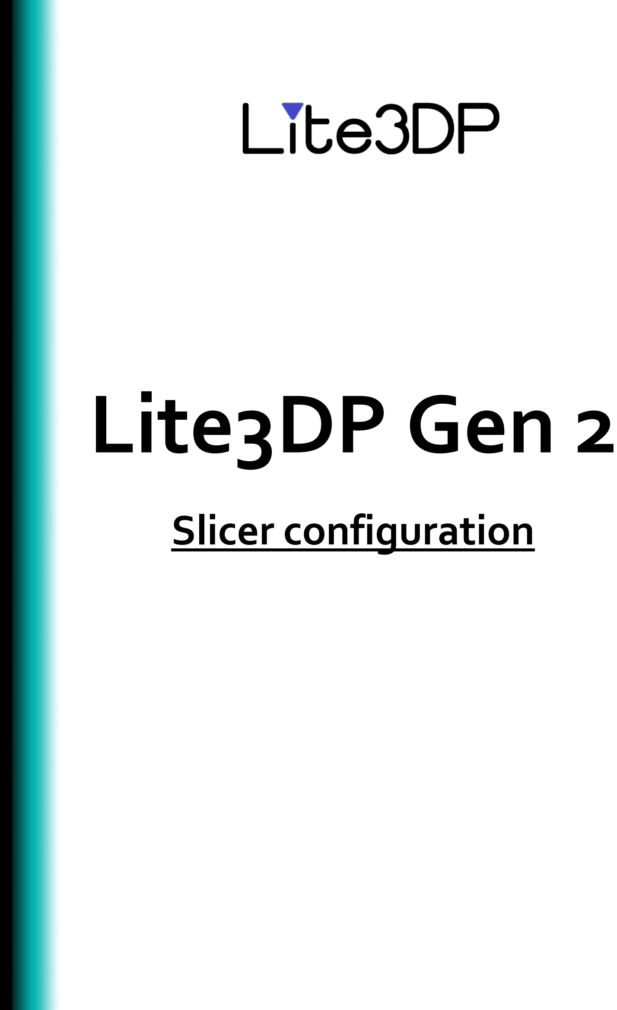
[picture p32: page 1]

# Lite3DP Gen 2

# Slicer configuration

# 1. CHITUBOX | page 2

# 2. PRUSASLICER | page 9

# 3. VOXELDANCE TANGO | page 14

# 4. LYCHEE | page 18

## 1. CHITUBOX

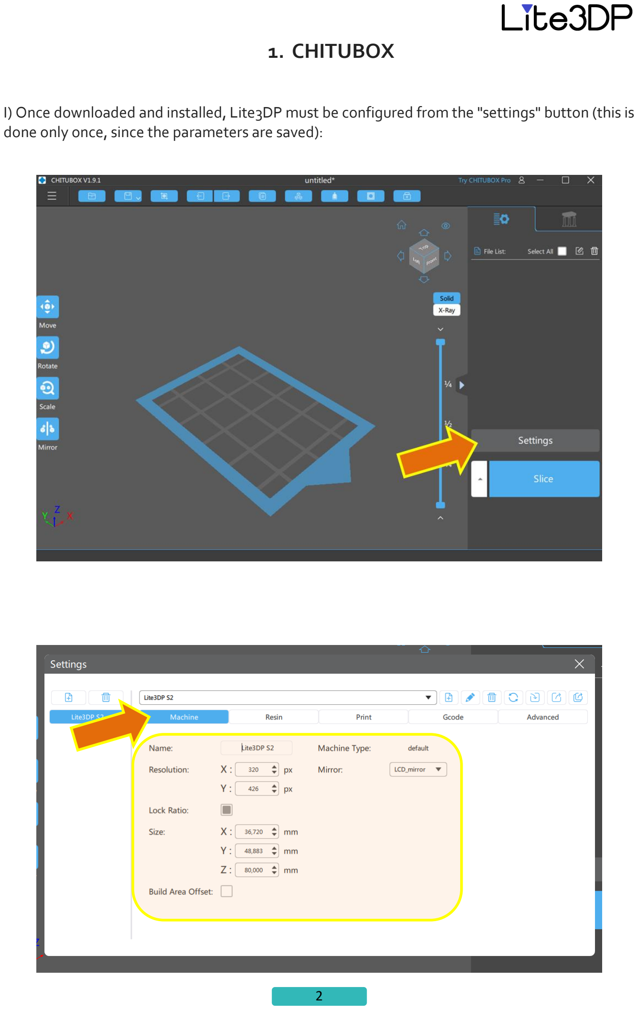
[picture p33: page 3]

I) Once downloaded and installed, Lite3DP must be configured from the "settings" button (this is done only once, since the parameters are saved):

Machine tab values:

Resolution:
X: 320, Y: 426

Size:
X: 36,720, Y: 48,883, Z: 80

Print tab value:

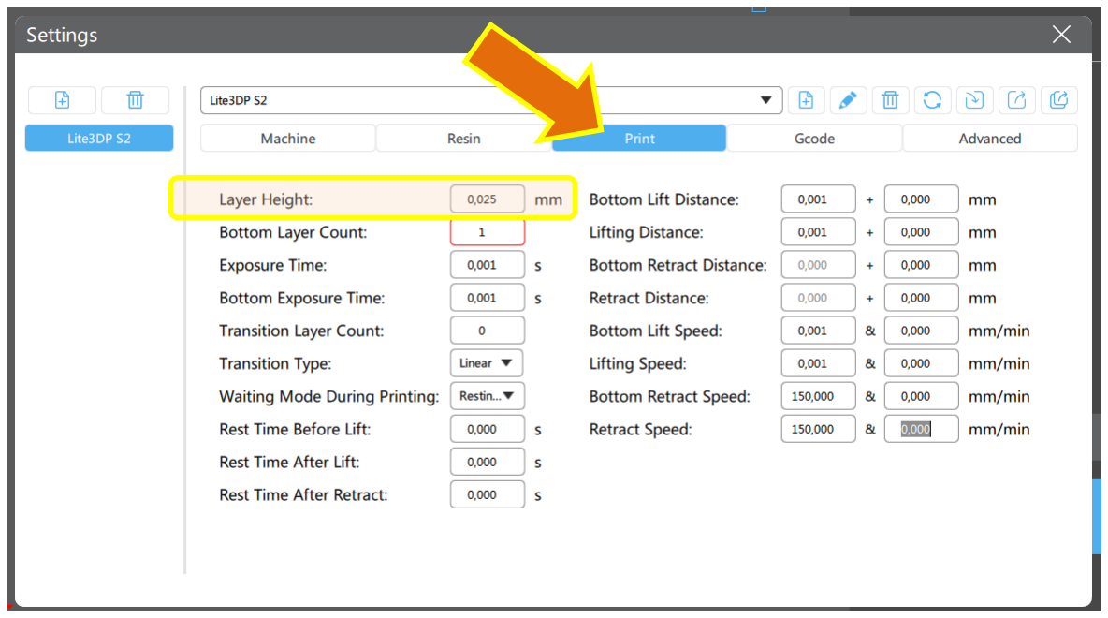
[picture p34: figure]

Only the Layer Height value should be changed, the other parameters will not affect the print job.

Files will always be processed with Layer Height = 0.025 mm.

(Lite3DP will allow you to select two other layer heights 0.05 and 0.1mm, which it will achieve by skipping images of the sections and of course moving a higher height).

Advanced tab:

Check "Anti-aliasing". Anti-aliasing level = 8.

This is it, and you will not need to modify these settings again.

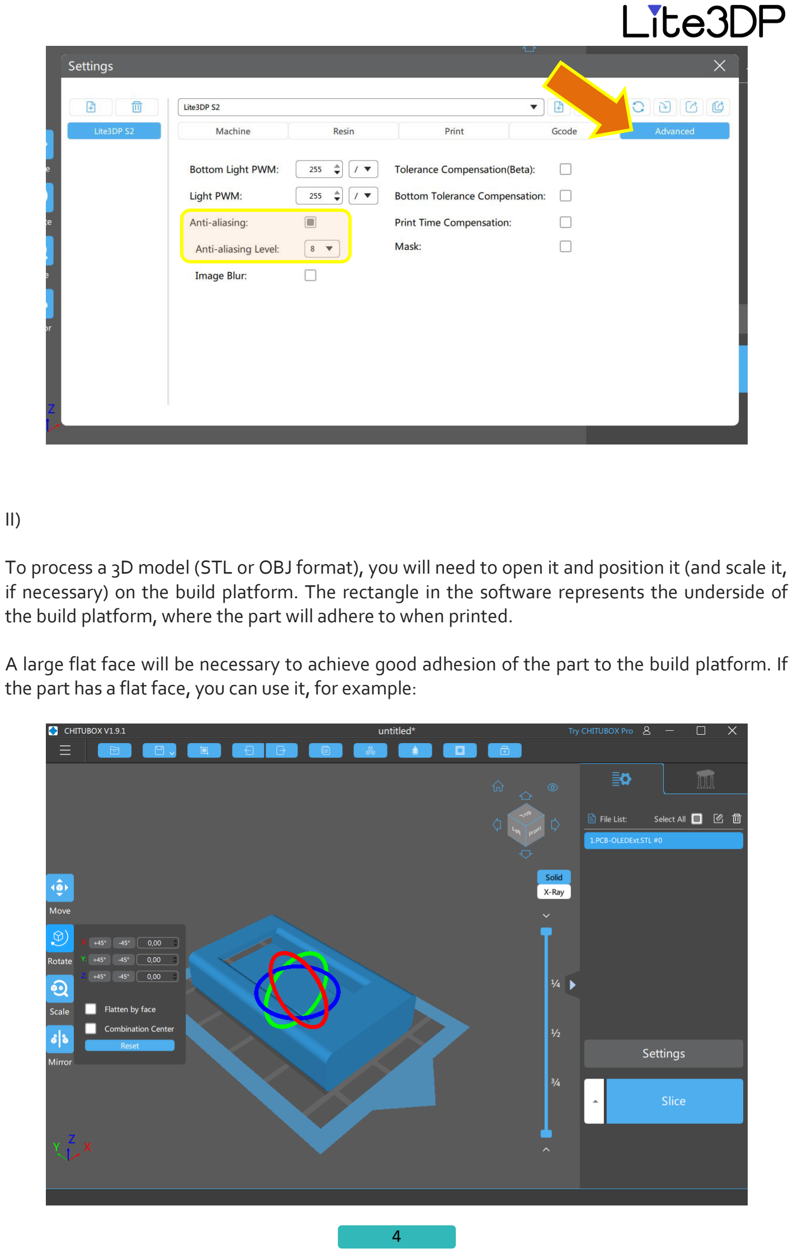
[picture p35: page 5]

II)

To process a 3D model (STL or OBJ format), you will need to open it and position it (and scale it, if necessary) on the build platform. The rectangle in the software represents the underside of the build platform, where the part will adhere to when printed.

A large flat face will be necessary to achieve good adhesion of the part to the build platform. If the part has a flat face, you can use it, for example:

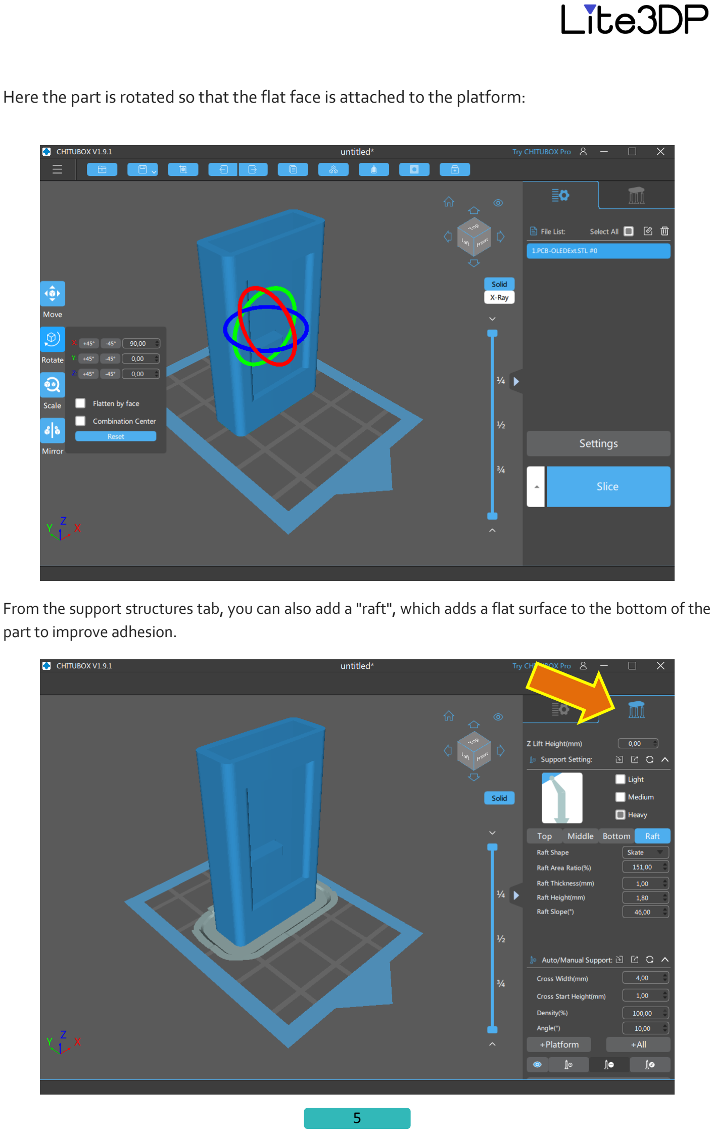
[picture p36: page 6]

Here the part is rotated so that the flat face is attached to the platform:

From the support structures tab, you can also add a "raft", which adds a flat surface to the bottom of the part to improve adhesion.

For complex models, where parts of it remain hanging, support structures must also be added in this same tab. For the first test prints, it is convenient to use simple parts with flat faces, to later increase the complexity.

About support structures and full functionality of Chitubox, a lot of literature can be found on the internet, it is the same as any MSLA machine.

Once the support structure is ready, we press the "Slice" button, which will generate the sections of the part (parallel to the plane of the build platform), with a spacing of 0.025 mm between them (due to the configured value of Layer Height).

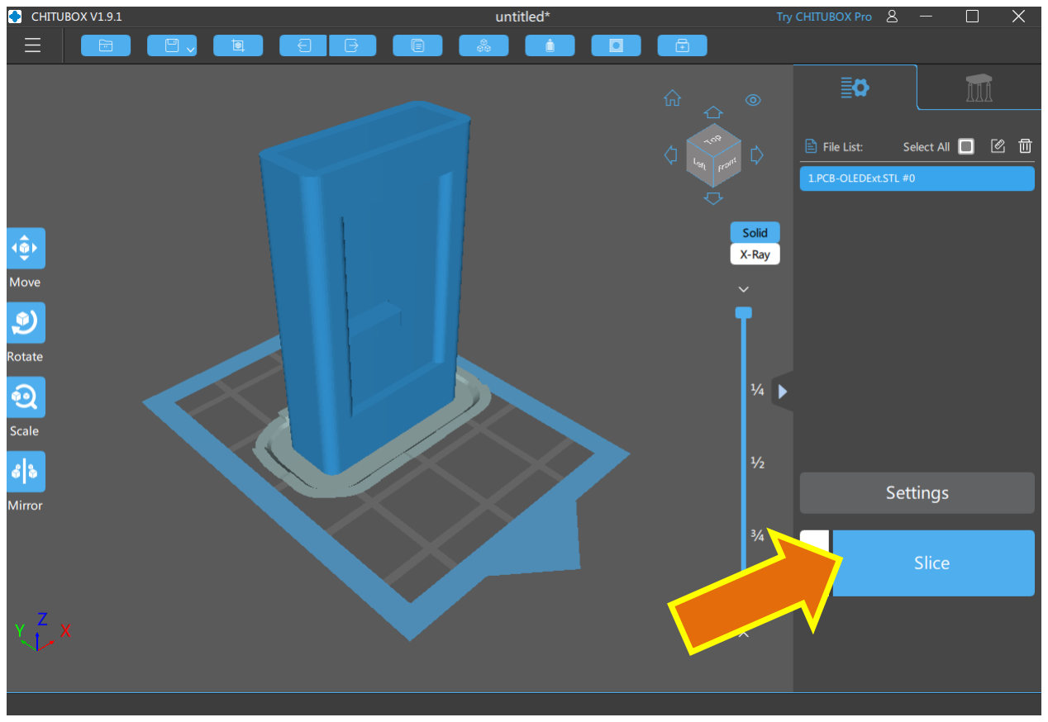
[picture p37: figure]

Here you can see and review the images of all the sections of the piece, also called "layers". If everything is fine, we press "Save" and choose the "Zip"format.

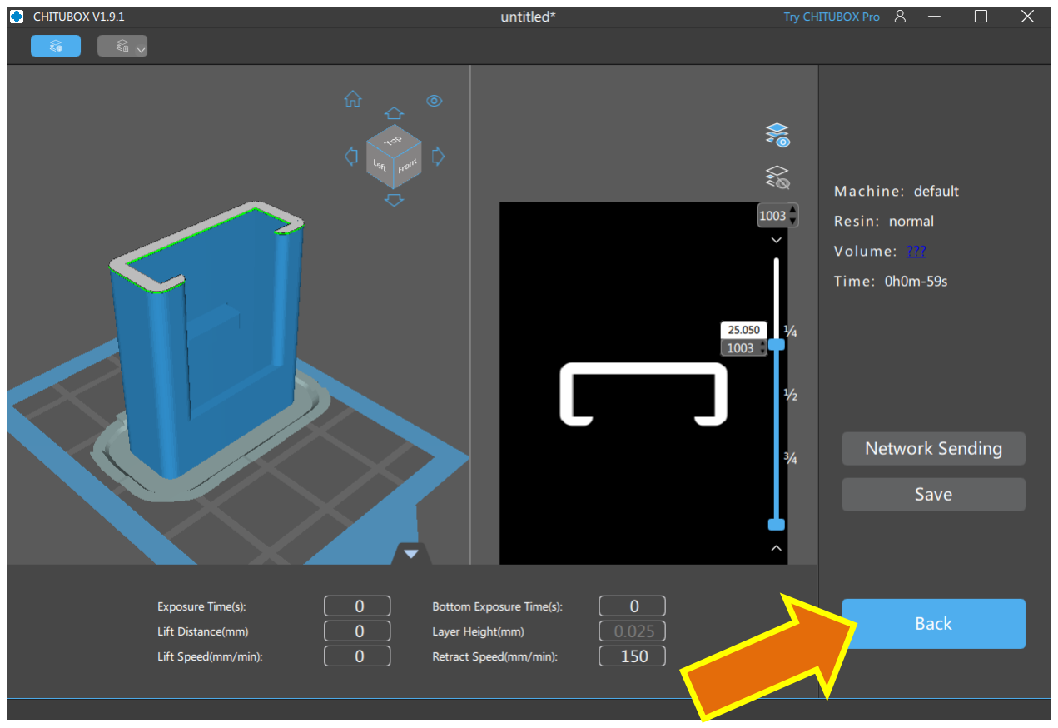
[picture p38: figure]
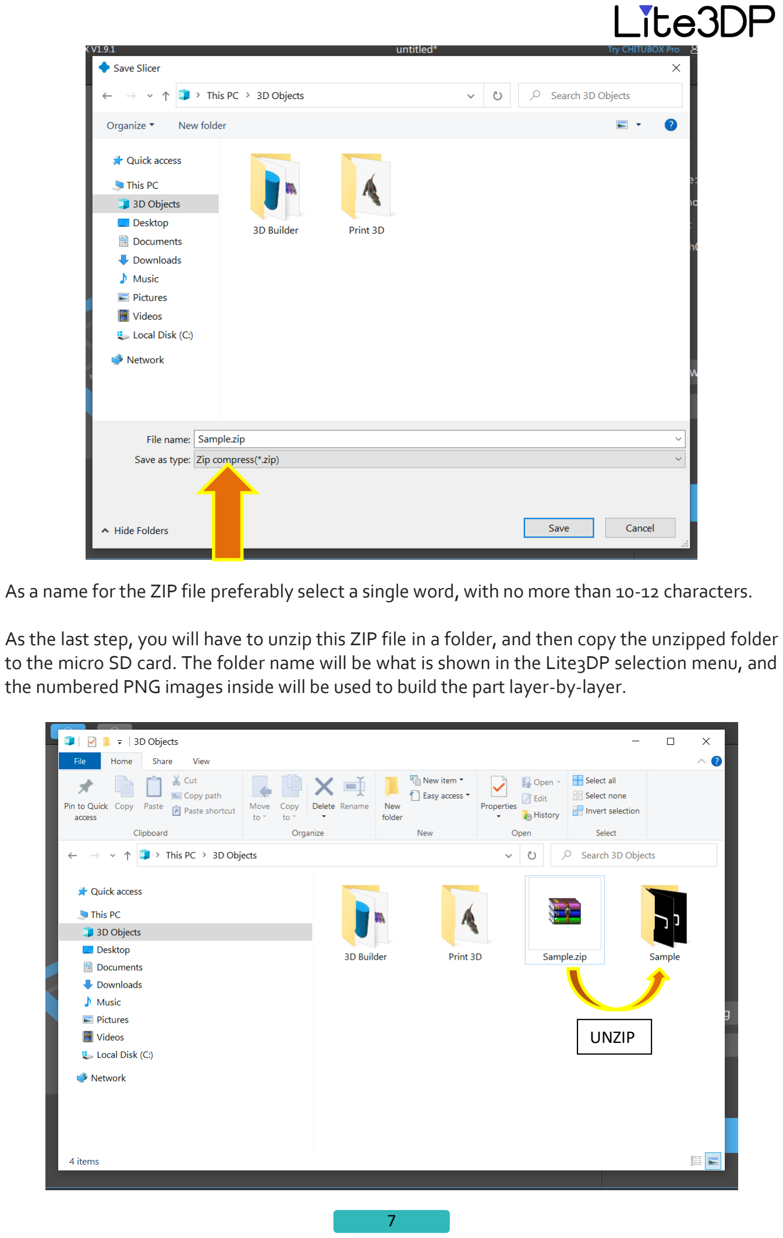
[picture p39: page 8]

As a name for the ZIP file preferably select a single word, with no more than 10-12 characters.

As the last step, you will have to unzip this ZIP file in a folder, and then copy the unzipped folder to the micro SD card. The folder name will be what is shown in the Lite3DP selection menu, and the numbered PNG images inside will be used to build the part layer-by-layer.

UNZIP

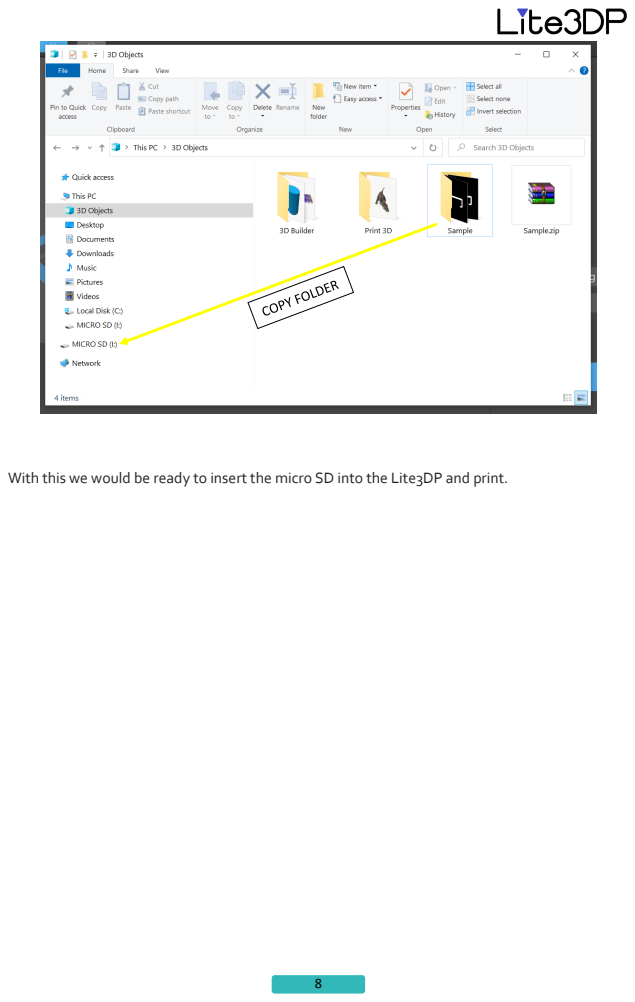
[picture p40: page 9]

With this we would be ready to insert the micro SD into the Lite3DP and print.

## 2. PrusaSlicer

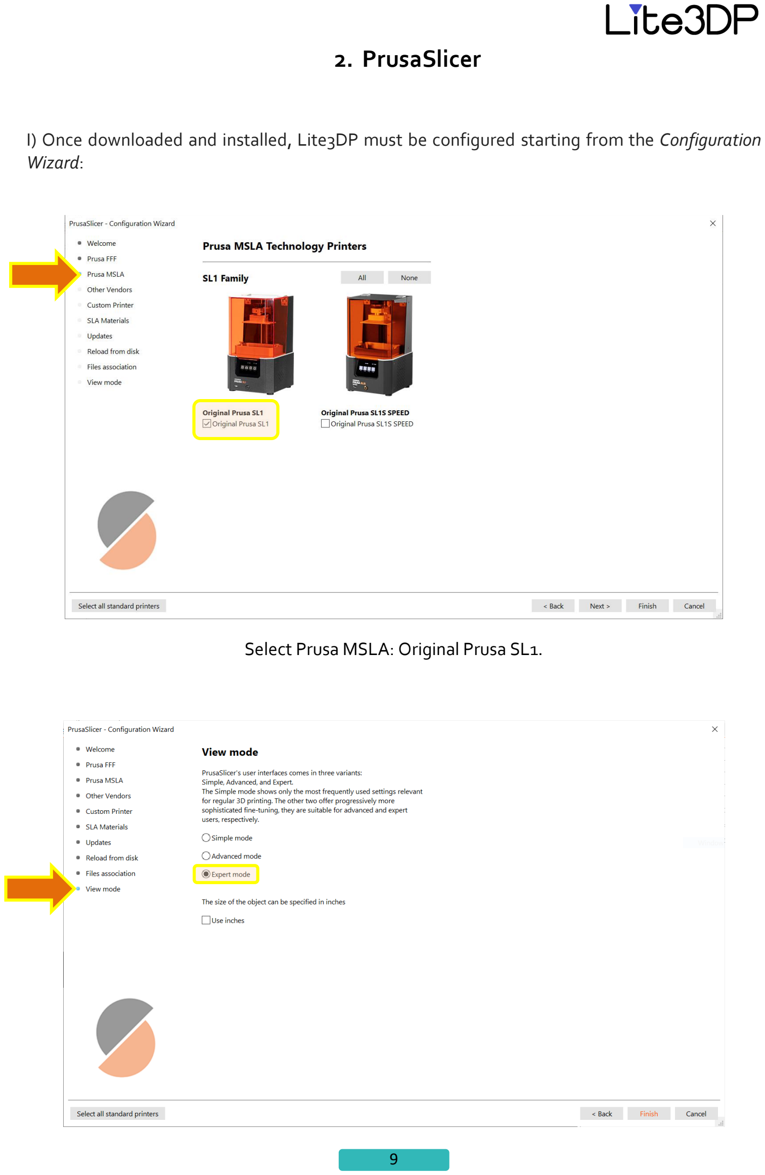
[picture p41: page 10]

I) Once downloaded and installed, Lite3DP must be configured starting from the Configuration Wizard:

Select Prusa MSLA: Original Prusa SL1.

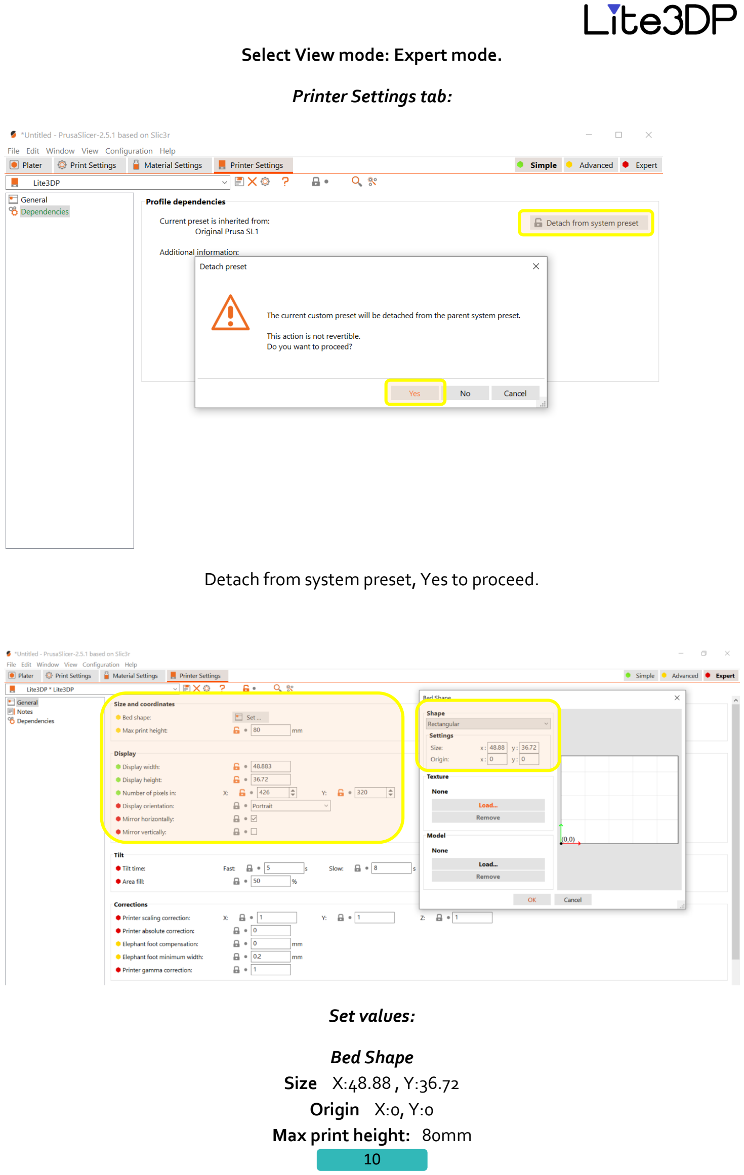
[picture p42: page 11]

Select View mode: Expert mode.

Printer Settings tab:

Detach from system preset, Yes to proceed.

Set values:

Bed Shape
Size X:48.88 , Y:36.72
Origin X:0, Y:0
Max print height: 80mm

Display
Display width 48.883 Display height 36.72 Number of pixels in: X:426 Y:320 Display orientation: Portrait Mirror horizonally: YES
Mirror vertically: NO

Print settings tab, Layers and perimeters. Layer height: 0.025mm

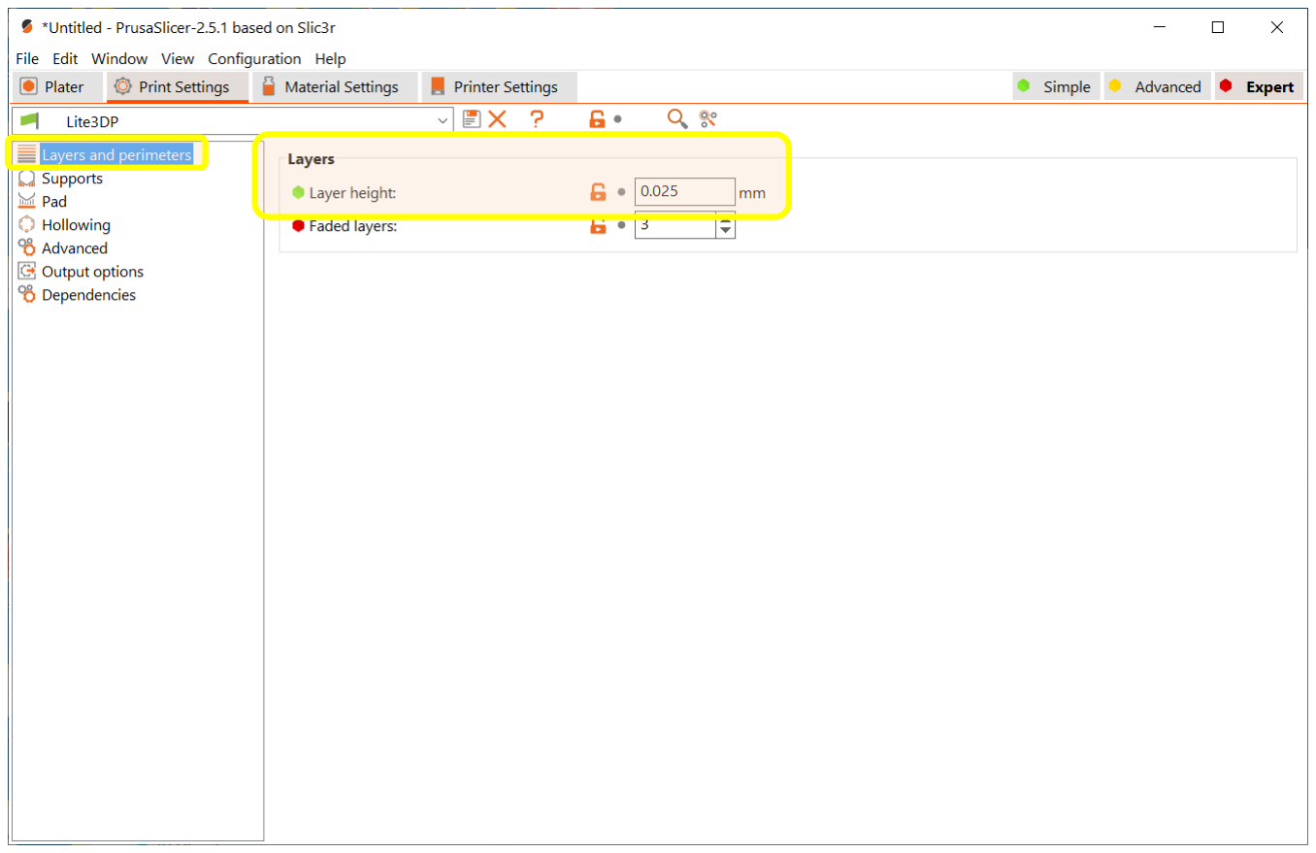
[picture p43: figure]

Print settings tab, Output options. Output filename format: .zip

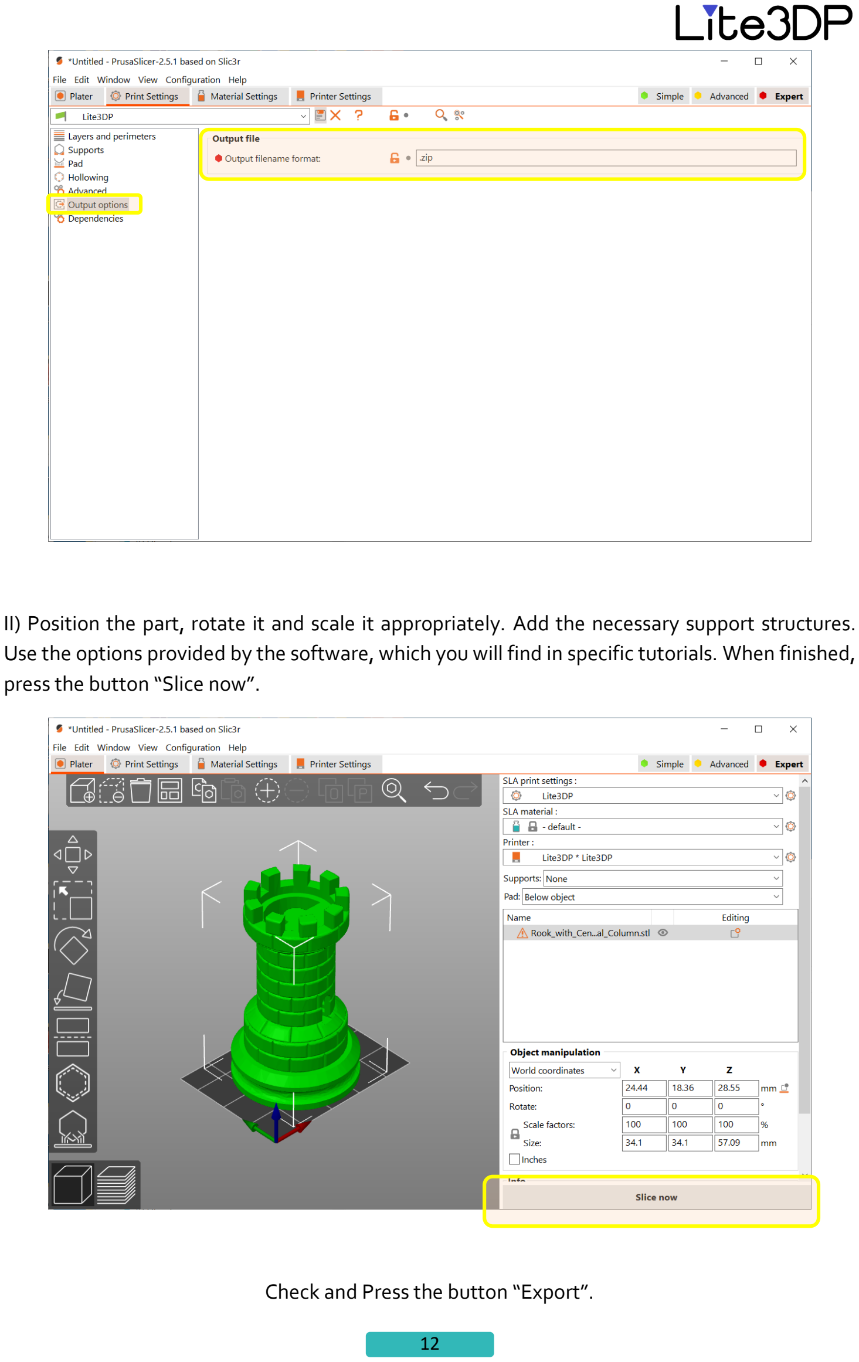
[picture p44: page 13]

II) Position the part, rotate it and scale it appropriately. Add the necessary support structures. Use the options provided by the software, which you will find in specific tutorials. When finished, press the button “Slice now”.

Check and Press the button “Export”.

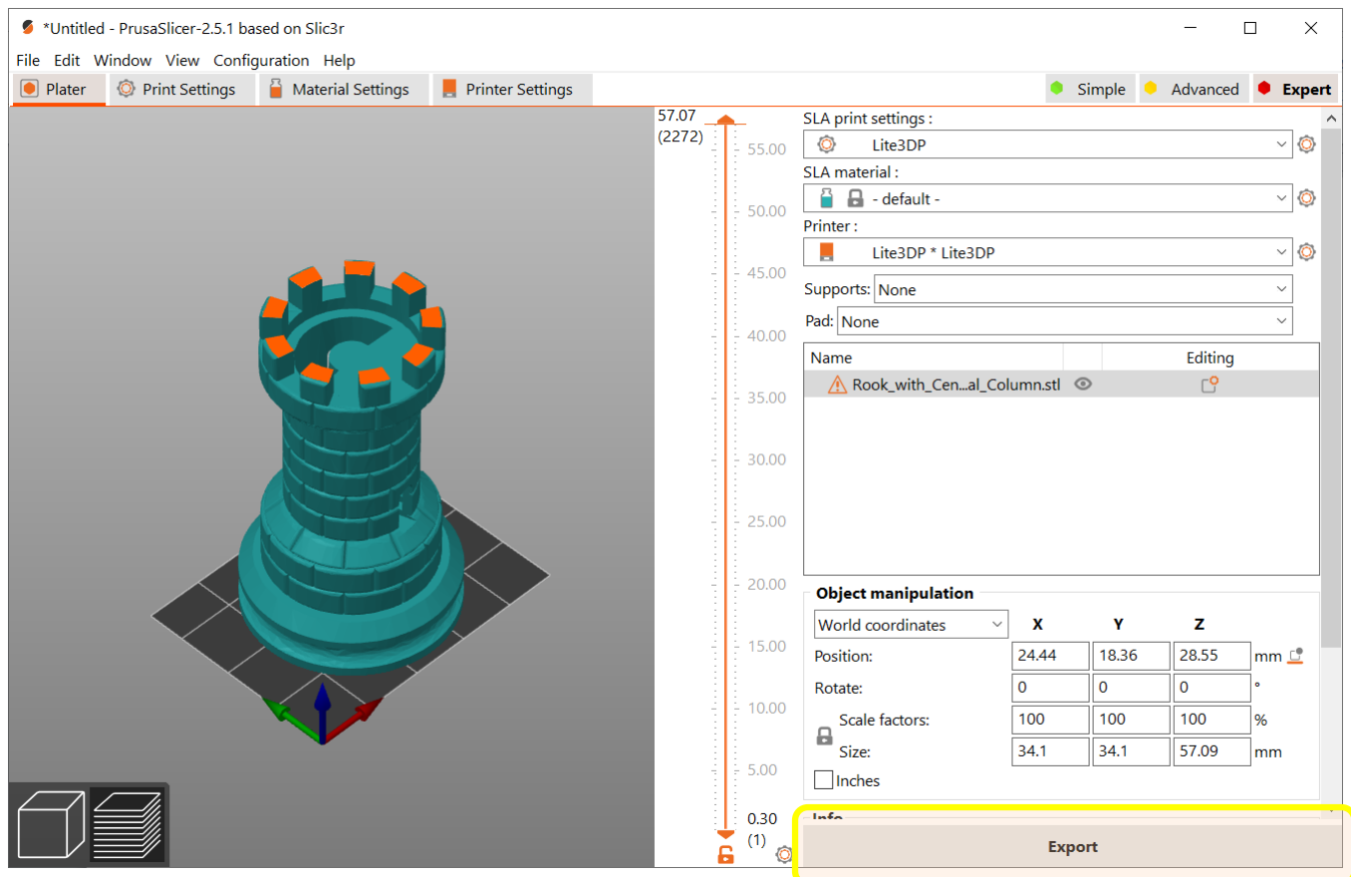
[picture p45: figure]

Save the Zip file with a short name with no more than 6 characters.

Unzip file and copy the unzipped folder to the micro SD card (see Chitubox section).

## 3. Voxeldance Tango

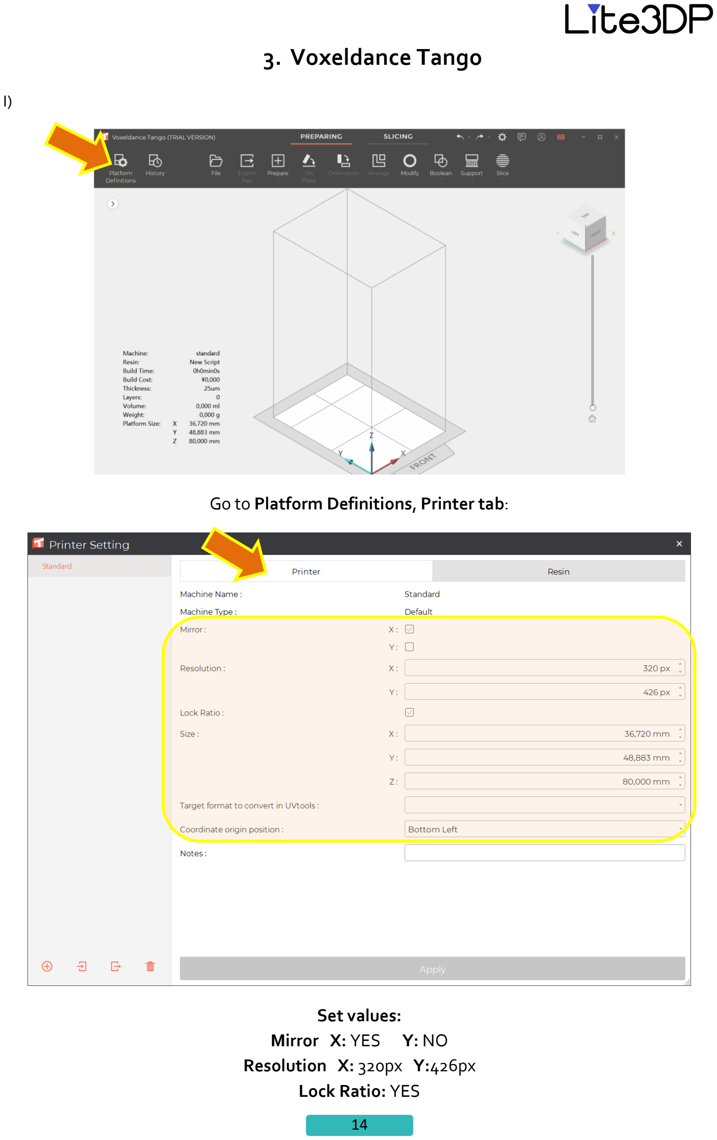
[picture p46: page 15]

I)

Go to Platform Definitions, Printer tab:

Set values:
Mirror X: YES Y: NO
Resolution X: 320px Y:426px Lock Ratio: YES

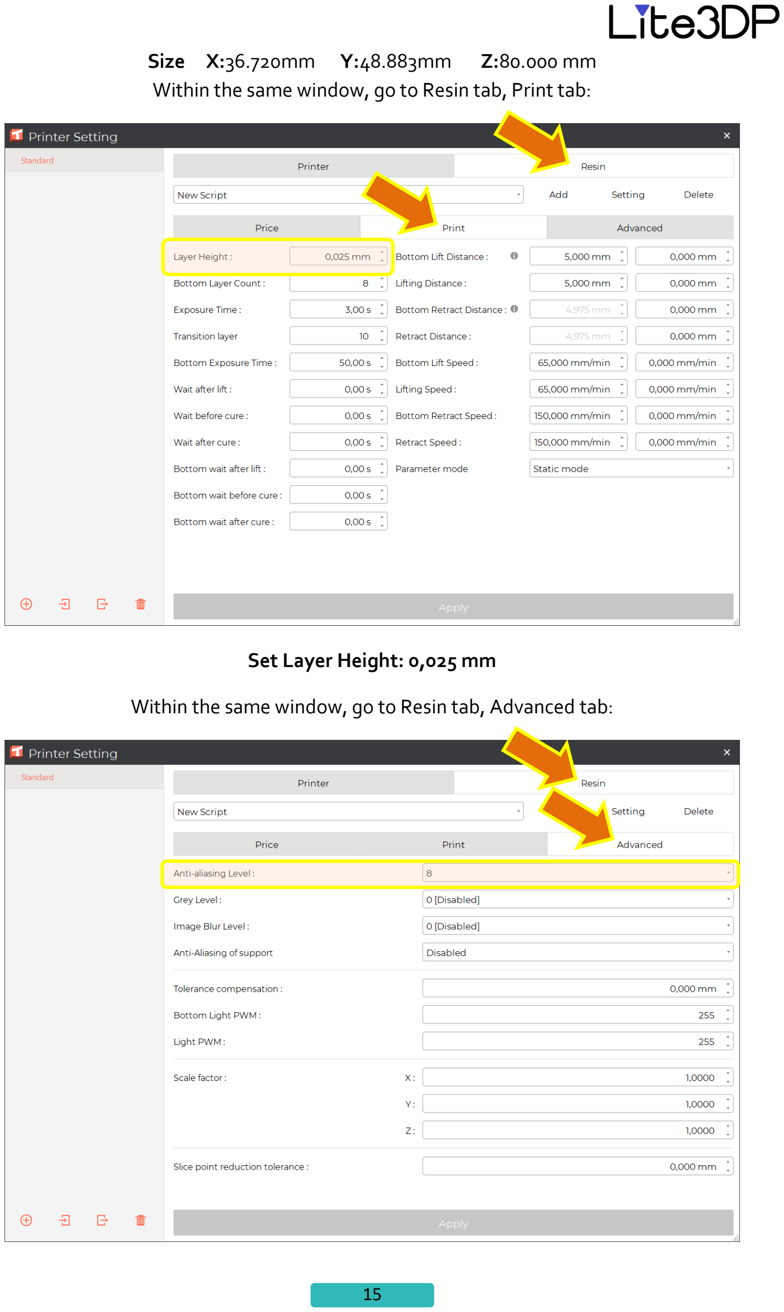
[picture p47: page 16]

Size X:36.720mm | Y:48.883mm | Z:80.000 mm
Within the same window, go to Resin tab, Print tab:

Set Layer Height: 0,025 mm

Within the same window, go to Resin tab, Advanced tab:

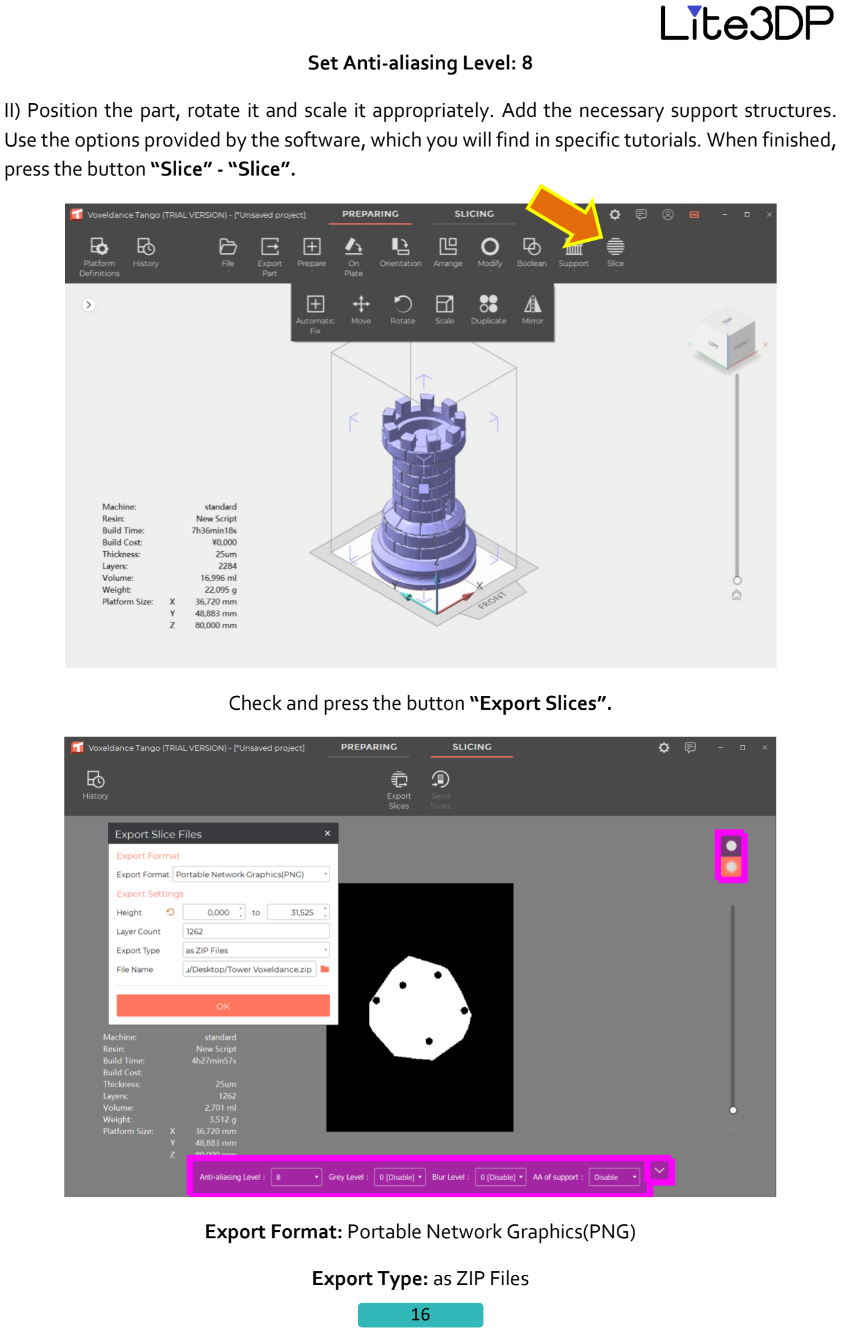
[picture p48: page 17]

Set Anti-aliasing Level: 8

II) Position the part, rotate it and scale it appropriately. Add the necessary support structures. Use the options provided by the software, which you will find in specific tutorials. When finished, press the button “Slice” - “Slice”.

Check and press the button “Export Slices”.

Export Format: Portable Network Graphics(PNG)

Export Type: as ZIP Files

Save the Zip file with a single word name, with no more than 10-12 characters.

Unzip file and copy the unzipped folder to the micro SD card (see Chitubox section).

## 4. Lychee

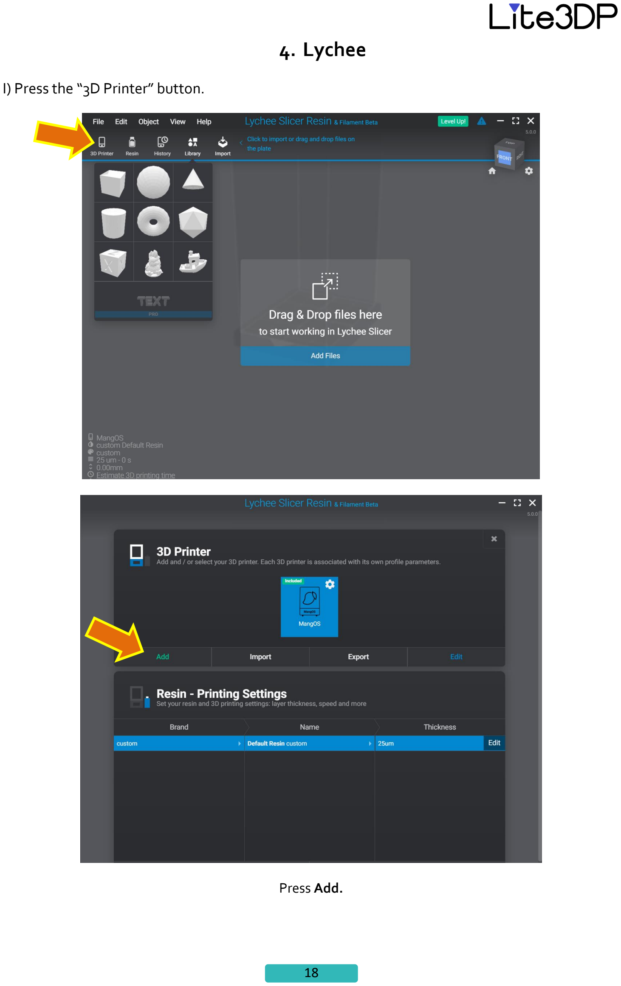
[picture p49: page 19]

I) Press the “3D Printer” button.

Press Add.

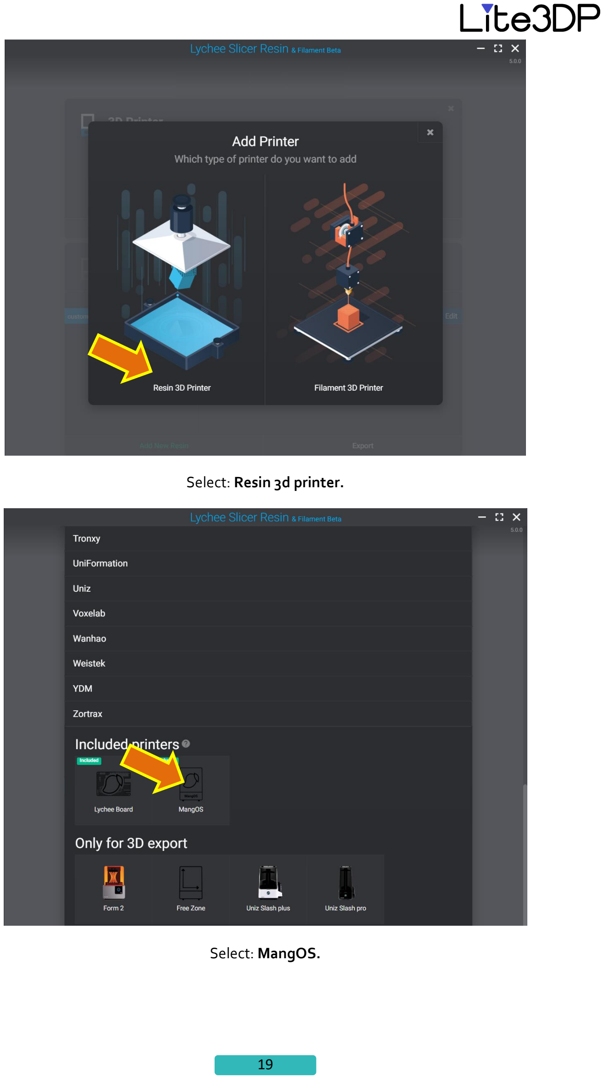
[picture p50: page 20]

Select: Resin 3d printer.

Select: MangOS.

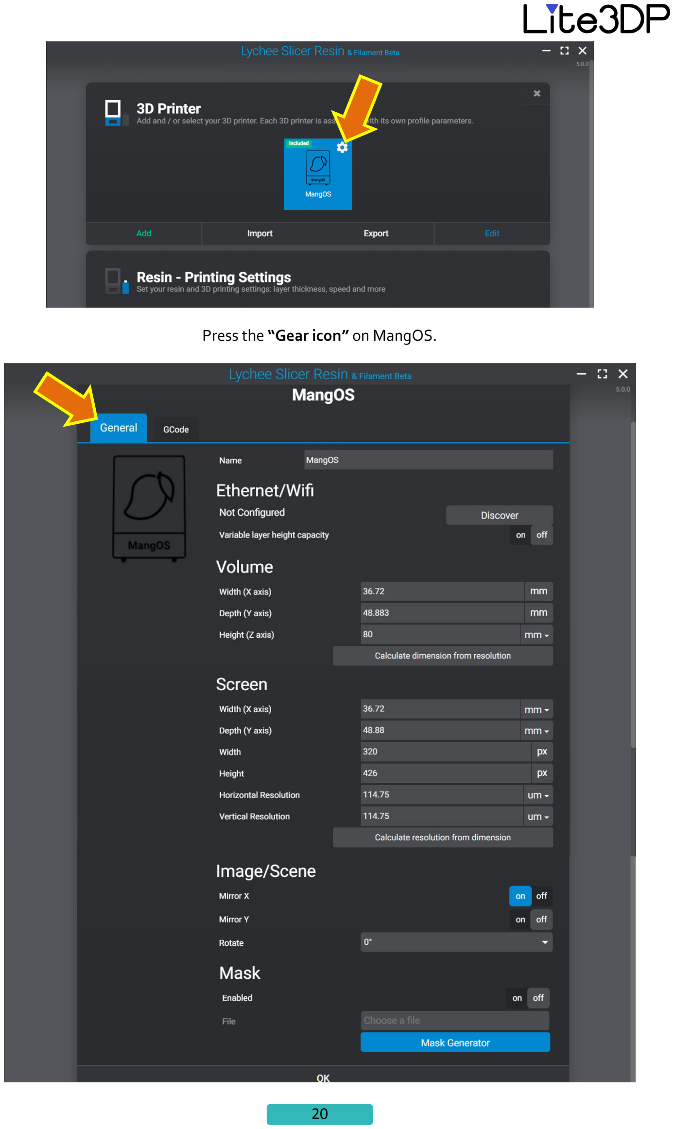
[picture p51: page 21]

Press the “Gear icon” on MangOS.

General tab. Set Values:

Volume
Width (X axis): 36.72 mm
Depth (Y axis): 48.883 mm
Height (Z axis): 80 mm

Screen
Width (X axis): 36.72 mm
Depth (Y axis): 48.88 mm
Width: 320 px
Height: 426 px
Horizontal Resolution: 114.75 um Vertical Resolution: 114.75 um

Image/scene
Mirror X: on
Mirror Y: off

Mask
Enabled: off

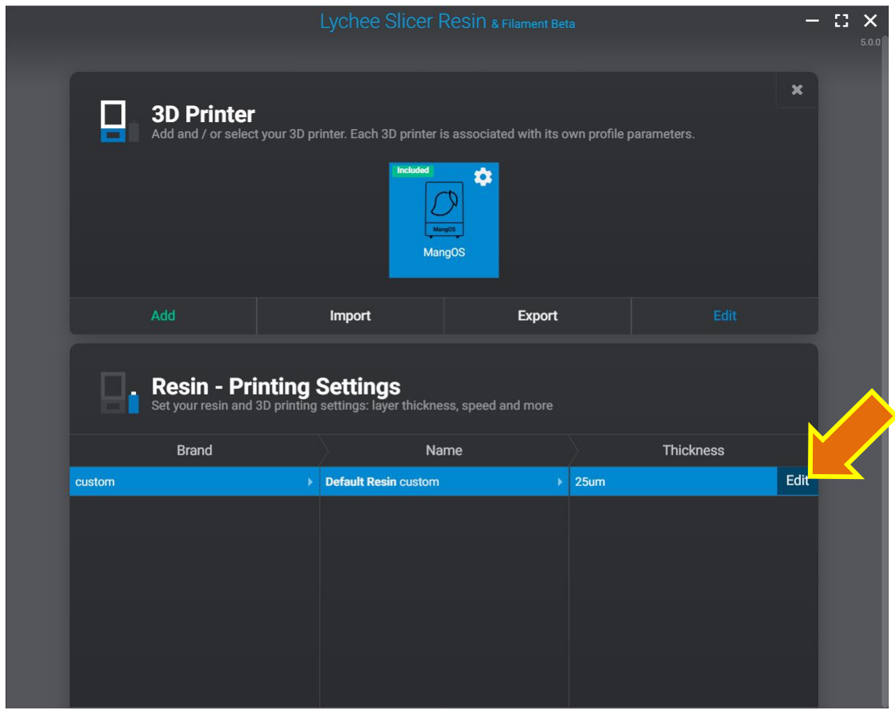
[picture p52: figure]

Resin – Printing Settings. Press Edit button.

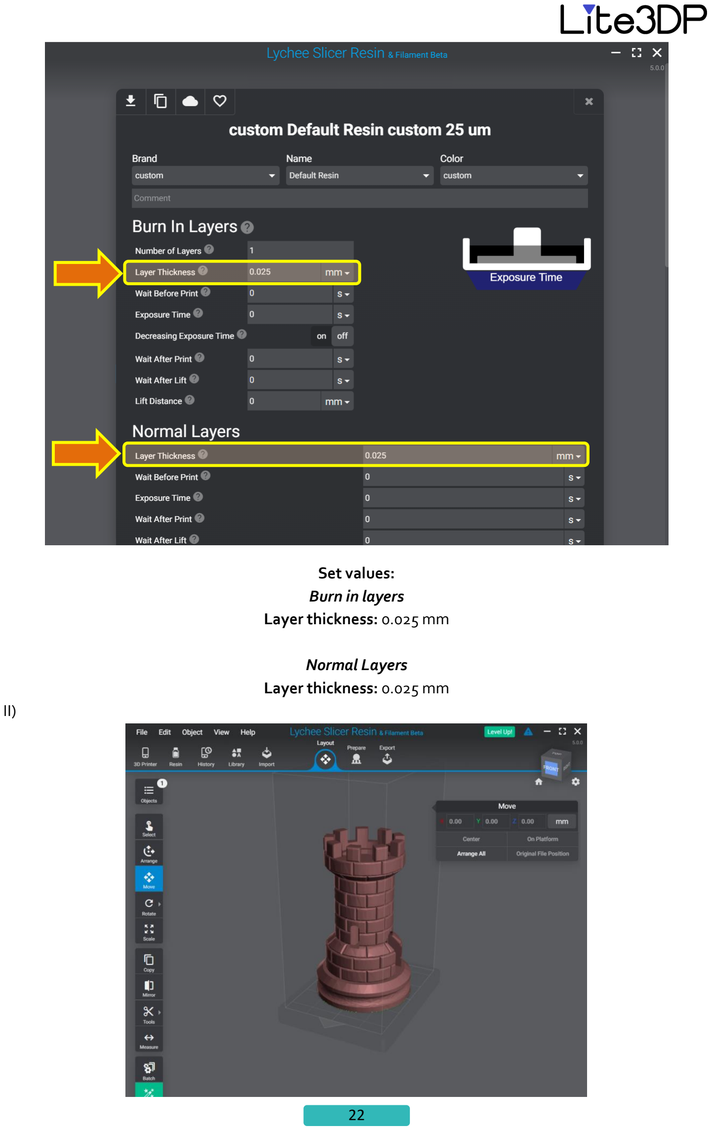
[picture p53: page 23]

Set values:
Burn in layers
Layer thickness: 0.025 mm

Normal Layers
Layer thickness: 0.025 mm
II)

Position the part, rotate it and scale it appropriately. Add the necessary support structures. Use the options provided by the software, which you will find in specific tutorials. Go through the tabs Layout-Prepare-Export.

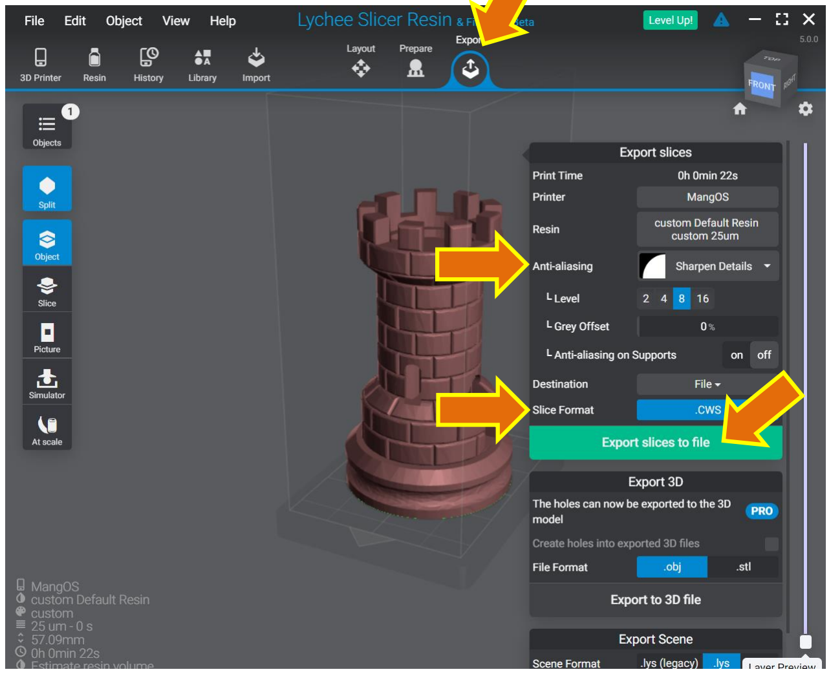
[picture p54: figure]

Export tab, select options: Anti-aliasing: Sharpen Details, Level 8. Slice Format: .CWS

Press the “Export slices to file” button.

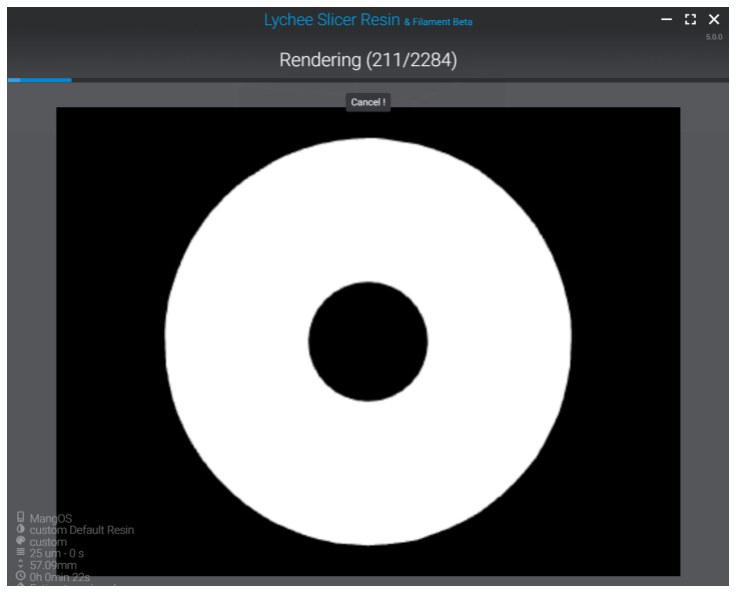
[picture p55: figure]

After all sections are rendered, a file with a .CWS extension will be created. In this special case, we will have to treat this extension as a .ZIP file. You can manually change the extension by deleting .CWS and writing .ZIP, or directly run the UNZIP to the CWS file. In both cases, a folder should be generated with the PNG images inside (if it also has other files, it is not a problem). Finally, copy the unzipped folder to the micro SD card.

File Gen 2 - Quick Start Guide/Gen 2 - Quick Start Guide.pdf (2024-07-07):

# QUICK START GUIDE

# Lite3DP Gen 2

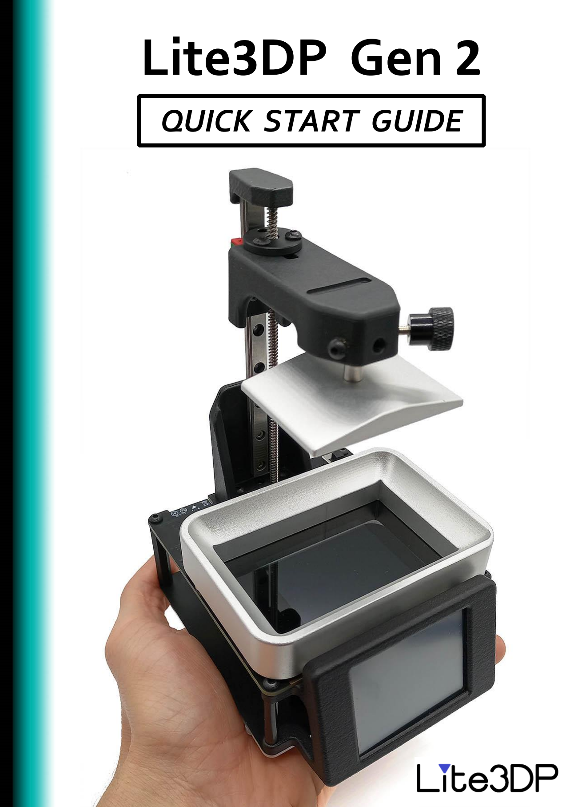
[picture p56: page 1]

## «Lite3DP Gen 2: Quick start guide»

## LITE3DP LLC

Copyright © 2024. All rights reserved.

First edition: July 2024.

## For more information, please visit:

## www.lite3dp.com www.github.com/Lite3DP

## For technical support, please contact:

## support@lite3dp.com

1. SAFETY PRECAUTIONS (page 2)
2. MSLA 3D PRINTING CONCEPTS (page 3)
3. INTERFACE (page 6)
4. BUILD PLATFORM LEVELING (page 8)
5. MAIN MENU (page 9)
5.1. «PRINT» SECTION (page 10)
5.2. «PARAMETERS» SECTION (page 13)
5.3. «TOOLS» SECTION (page 18)
6. POST-PROCESSING (page 20)
7. RELEASE FILM INSTALLATION (page 21)
8. SLICING (page 23)
9. BEFORE STARTING (page 25)
10. TROUBLESHOOTING (page 26)
11. MINI RESIN VAT & BUILD PLATFORM (page 29)
12. USER NOTES (page 31)

## 1. SAFETY PRECAUTIONS

First of all, please read the safety information sheet included with the machine and keep it for future reference.

Follow the safety data sheets for 3D printing resins, isopropyl alcohol, and all chemicals you use with the Lite3DP. Nitrile gloves, eye protection and a well-ventilated environment are necessary. If the LCD printing display is exposed, do not look directly at the UV light.

The Lite3DP should not be exposed to direct sunlight or contacted by conductive elements such as metals. It should be used on a flat, non-conductive surface.

The Gen 2 features an auxiliary connector with voltage and communication pins with the microcontroller. Any incorrect connection may cause permanent damage to the main board. Please only manipulate the auxiliary connector pins if you have adequate knowledge and at your own risk. The same applies to connecting the CP2102 auxiliary board and uploading new firmware.

The machine is not designed to be powered by a USB port (it is only used to upload firmware), it must be connected to an external 12 V DC power supply and a minimum current of 1000 mA, with a 5.5*2.1 mm diameter cylindrical connector. Any external power supply used with Lite3DP Gen 2 must comply with relevant regulations and standards applicable in the country of intended use.

Immediately replace the vat release film if there is any sign of breakage, wear or leaking. CAUTION: Leaking resin into the machine can cause permanent damage.

## 2. MSLA 3D PRINTING CONCEPTS


High power
405nm UV LED

Section image displayed

Build platform

Carriage

MSLA 3D printing is based on the principle of solidifying, layer by layer, a photosensitive resin using a UV light source. On each layer, an image corresponding to the section of the part to be printed is displayed. UV light passes only through the displayed section for a certain exposure time, solidifying the resin into its shape.


The first solidified section adheres to the build platform, and all the rest to their previous one. After the solidification of a layer is complete, the build platform rises to peel off the model from the release film (FEP/NFEP/ACF) and allow a new layer of liquid resin to form. When the platform descends, it is located at a distance from the release film equal to the layer thickness, to continue with the solidification of the next layer.

For each layer thickness and for each different resin, the appropriate values of printing parameters must be assigned: exposure times, build platform lift heights, speeds, among others (see section 5.2).

## 2. MSLA 3D PRINTING CONCEPTS

In order to get a successful MSLA 3D print you will need:

### 1. Preparation of the build platform and the resin vat

The preparation of the build platform consists of completing the leveling procedure (see section 4, build platform leveling).
The resin vat must contain resin, in a minimum quantity to form a continuous layer on the release film and in a maximum recommended quantity corresponding to the vat inner step (~2-7 cm

3
for mini vat, ~ 6-40 cm

3
for standard vat):


### 2. Generation of the print-job sections

The images of the sections are obtained from a slicer software. For each model to be printed, you must have a folder with numbered images in PNG format (320*426 px) in the micro SD memory (see section 8, slicing).

### 3. Configuration of the printing parameters

Twelve parameters must be configured appropriately for each resin and layer thickness to be used. This can be done from the main “Parameters” section or just before finishing the “Print” section workflow. Six memories are included to store the set of parameters. (see section 5.2).

## 2. MSLA 3D PRINTING CONCEPTS

## 3. INTERFACE

Power button

Micro SD card slot

Play/pause button


The Play/Pause button has the following functions:

1. By keeping it pressed on the initial "PRINT" screen, you can manually raise the platform in case of an unforeseen event. CAUTION: the machine does not have an upper endstop, be careful not to hit the bearing support.
2. Allows you to stop the preview of the sections, after choosing the file to print.
3. Allows you to pause the print job by holding it down until the current layer finishes. When you pause, the platform will rise, revealing the part being printed. Printing resumes when you press it again.
4. Starts the print job and the vat cleaning process.

## 3. INTERFACE

OLED; TOUCH; BACK; NEXT; DOWN; OLED auxiliary display: Shows the progress of the print job and additional information.; Touchscreen display: Allows intuitive menu navigation using on- screen arrows, as well as available options.; On selection screens like the one shown above (and the confirmation screens), pressing the box/center of the screen is equivalent to the NEXT arrow.; Capacitive touch buttons for navigation of the menu displayed on the main screen.

## 4. BUILD PLATFORM LEVELING


Calibration card

The platform must be level before starting a print job.
When leveling, it is ensured that the build platform has its flat surface parallel to the glass of the mask display, at a distance equal to the thickness of the release film and firmly secured by adjusting the hand knob tightening screw.

For leveling, release the hand knob screw, hold the build platform on the carriage magnet and place the leveling card on the display (two thicknesses are included, the thinner one for NFEP/FEP films and the thicker one for ACF films). Before starting, arrange the platform so that its flat side is as parallel as possible to the display. At the end of the descent, with the UP and DOWN arrows, you can fine-tune the distance of the platform, so that it is just above the calibration card. This value is stored in the permanent memory for subsequent leveling. If the platform is too tight, it will collide with the display. If it is too loose, the initial layer will not adhere to the platform.

## 5. MAIN MENU


Start printing workflow.

Adjust printing parameters and optionally store them
in memories (A-F).
Access | the | resin | vat
cleaning tool and factory
test. The first allows a layer of resin to solidify on the release film to facilitate cleaning of adhered solid
pieces.

## 5.1. «PRINT» SECTION


LEVEL PLATFORM

LEVEL

SKIP

LEVEL PLATFORM

PLACE PLATFORM
AND SPACER

The workflow begins
with leveling the build
platform. Only skip this
step if leveling was
previously completed
and was not used for
printing.

See section 4: build
platform leveling.

See section 4: build
platform leveling.

## 5.1. «PRINT» SECTION


FILE

MICRO SD

TEST PRINT

SELECT FILE

Preview

Here you can access two
test files included in the firmware, or proceed to
perform a normal print
from the micro SD card.
Note: The test files have
two fixed parameters:
Bottom layers=5 and
Transition layers=0.

Select the name of the
folder with the sections
saved | in | the | root
directory of the micro SD
card.

A quick preview of sections of the selected file is shown here. Interesting note: in this preview and during
printing, the sections shown on the touchscreen display have the same shape and
size as those shown on the mask display for printing.

## 5.1. «PRINT» SECTION


PARAMETERS

Current parameters

CONFIRMATION 1-2-3

….

….

….

….

DETAILS

FOLDER: …..
TOTAL LAYERS: …..
EST. TIME: |

PRESS START!

If the build platform is level, a correct preview was displayed and the parameters were
selected, place the vat with resin and press the START
/PAUSE button. (The estimated time here is an approximation and will be refined after the transition layers).

A summary of the selected
parameters is displayed on
the | three | confirmation
screens.

The printing parameters are selected here: current (the set of parameters last
modified), change them
(which allows you to modify the 12 parameters) or the
set of parameters stored in the memories (A-F).

## 5. 2. «PARAMETERS» SECTION

1. LAYER HEIGHT

100 um

2. INITIAL EXPOSURE

40 s

3. EXPOSURE TIME

6.0 s

The height of a single layer
affects | printing | time:
thinner | layers | require
shorter | exposures | but
result in more layers,
making the overall printing time longer.

The printer uses longer
exposures for the initial
layers to improve adhesion to the build platform.
Longer | bottom | layer
exposure enhances model
adhesion. (An excess will
cause oversized sections).

Normal layer exposure
time, which determines
how long resin is exposed
to UV light to cure a layer, is crucial for the quality and success of a 3D print.

## 5. 2. «PARAMETERS» SECTION


4. UV POWER

255

5. BOTTOM LAYER COUNT

4

6. TRANSITION LAYERS

0

Change the output power
of the UV LED (0-255).
More power means faster
curing of the resin.

This parameter determines
the number of layers
exposed with a higher
initial exposure time to
ensure a strong foundation that adheres well to the
build platform.

Transition layers gradually
reduce | exposure | time
between the bottom and
normal layers, ensuring a
smooth shift in curing
times.

## 5. 2. «PARAMETERS» SECTION


7. BOTTOM LIFT HEIGHT

6.00 mm

8. LIFT HEIGHT

4.00 mm

9. BOTTOM LIFT SPEED

0.70 mm/s

Lift height is the distance the build platform moves
up between layers to
separate | the | printed
model from the release
film. For the bottom
layers, a 50% higher height is recommended.

The ideal lift height should be sufficient to peel the
printed model from the
release film.

Lift speed determines how
quickly the build platform rises after curing each
layer, which also dictates the speed at which the
model is peeled off the
release film. A very slow
speed is recommended for
the bottom layers.

## 5. 2. «PARAMETERS» SECTION

10. LIFT SPEED

1.70 mm/s

11. RETRACT SPEED

2.90 mm/s

12. REST TIME

0 ms

Begin with a slower lift
speed initially. As you gain confidence and achieve
consistent good prints,
feel free to experiment
with faster lift speeds.

Retract speed is the rate at which the build platform
descends into the resin
vat. This speed generally
has minimal impact on
print quality, but if the
speed is high the motor
will be noisier.

This parameter introduces
a delay in exposure after
the build plate retracts to
its | lowest | position,
allowing the liquid resin to
settle | and | form | a
continuous layer between
the model and the release
film.

13. STORE PARAMETERS; DO NOT STORE

Here you can store all of the 12 previous parameters in
one of the 6 permanent
memories (A-F). The selected
parameters | are | kept | as
"current parameters" until they are modified again, even if they are not stored in the memories.

## 5. 2. «PARAMETERS» SECTION

## 5.3. «TOOLS» SECTION


TOOLS

CLEAN RESIN VAT

FACTORY TEST

CLEAN RESIN VAT

EXPOSURE TIME (s): 45

PRESS START!

EXPOSURE TIME

45 s

With the "clean resin vat" tool you can solidify a thin layer of resin at the
bottom of the vat. This
layer | can | be | easily
removed, taking with it
the impurities stuck to the release film.

The exposure time must
be long enough to cure a
continuous layer of resin. (It has a value similar to or slightly higher than an
"Initial exposure" for a 100 um layer).

Summary screen. Place
the vat with enough resin
and | press | the
START/PAUSE | button.
During the selected time,
a blank screen will be
displayed and the UV light will be turned on at full
power.

TOOLS; CLEAN RESIN VAT; FACTORY TEST

The | "factory | test" is
designed to test the
correct operation of the
machine after assembly.

FACTORY TEST; REMOVE TRAY AND PLATFORM; PRESS START!

Before starting, remove
the resin vat and the build
platform | from | the
machine. | Press | the
START/PAUSE button and
follow the instructions on the screen.

## 5.3. «TOOLS» SECTION

## 6. POST-PROCESSING

After printing is finished:

- Remove the printed parts from the build platform with a spatula, leaving it completely clean for the next print.
- Check the resin vat, and eliminate any remaining solid pieces adhered to the release film or floating impurities. This is especially important if the print failed for some reason. If necessary you can use the “Clean resin vat”tool.
CAUTION: A dirty vat resin will prevent proper printing and may cause damage to the machine.
- Wash the printed parts inside and out with isopropyl alcohol or water, depending on the resin used. There should be no liquid resin left on the surface.
- Complete the curing of the parts by exposing them to 405nm UV light in a suitable cabin, or inside a transparent container filled with water exposed to sunlight.

## 7. RELEASE FILM INSTALLATION


Film

Press the frame
to insert the film
as much as
possible
Puncture the film into frame holes | Insert the screw and tighten slightly

## 7. RELEASE FILM INSTALLATION


Continue with the opposite screws, lightly tightening

Once all the screws are in place, tighten sequentially. Cut the excess film with a box cutter.

## 8. SLICING

Before starting a print job, the model(s) must be sliced. To do this, you must use a slicer software: Prusa slicer, Voxeldance Tango, Chitubox, Lychee, etc. The only requirement for a slicer to be compatible is that it can output a compressed file (e.g., ZIP or CWS format) containing PNG images of the sections with one of the following name formats:

Lychee: lychee0000.png, lychee0001.png, ...; or lychee000.png, lychee001.png, ... Prusa slicer: foldername00000.png, foldername00001.png, ...
Voxeldance Tango: 0.png, 1.png, ...
Chitubox: 1.png, 2.png, ...

The output files of the slicers must be unzipped and the obtained folders copied to the root directory of a micro SD card (The card must be in FAT32 format). The names of these folders are the ones that Lite3DP will show for selection in the PRINT section. (Note: For CWS format files (Lychee slicer), you can manually change the extension “.CWS” to “.ZIP” and proceed to unzip them normally).


(…)

## 8. SLICING

To configure any Slicer software, the values in the previous table must be used. These are constants and should not be modified. You should always process files with layer height equal to 0.025 mm (when selecting 0.05 or 0.10 mm layer height, Lite3DP skips images during printing). The values of the other printing parameters included in the slicers will not affect the print job, since these are selected on the Lite3DP menu.

(For more details, a Slicer configuration guide is available on our Github).

Please review the documentation for the slicer of your choice. To achieve correct processing, you must open the 3D model(s), position and rotate them in relation to the build platform, generate the appropriate support structures and finally obtain the output file.

Mini resin vat note:

No changes should be made to the configuration. You just have to make sure that the model is centered on the build platform and its size does not exceed 20 x 20 x 80 mm.

| CONFIGURATION
LAYER HEIGHT | 0.025 mm
RESOLUTION (px) | X: 320 Y: 426
BUILD VOLUME | X: 36.720 Y: 48.883 Z: 80

## 9. BEFORE STARTING

Before first use:

- Install the release film on the resin vat according to section 7. Then, it is recommended to first fill the vat with water for half an hour and check that there are no leaks.
- Make sure to remove the transparent protective film from the mask display.
- Verify that the magnets are correctly located, so that when holding the vat, the release film is in contact and rests evenly on the mask display. If not, improve the location of the magnets until the vat is inserted correctly. (See section 10).
- Make sure your Micro SD card is formatted in FAT32.
- Verify that by adjusting the carriage hand knob screw, the platform is firmly attached.Otherwise, please see section 10.

Before every use:

- Verify that the vat has no solid residue or damaged release film. At the slightest sign of damage, please replace the film. (As a tip, only use the plastic spatula to mix the resin and never exert any pressure on the release film, as it deforms and marks easily).
- Perform proper cleaning and leveling of the platform.

## 10. TROUBLESHOOTING

Print issues

The Lite3DP Gen 2 is a very special 3D printer, but it shares the same printing recommendations with all other MSLA 3D printers. Nowadays there is abundant online information about common problems with this technology, from which you can learn typical causes and solutions.

We will not go into details here, but we can mention the typical causes of failures:

- Incorrect platform leveling.
- Resin vat with problems: dirty/expired/poorly mixed resin, dirty/damaged release film.
- Incorrect selection of parameters: Insufficient/too long exposure times. Very high lift speeds. Insufficient lift height. Insufficient bottom and/or transition layers.
- Defective slicing: poor positioning or orientation of the parts, insufficient/incorrect support structures, incorrect hollow, among others.
- Damaged Micro SD card or not formatted to FAT32.

In most cases the solutions are experimental, they must be solved through trial and error.

## 10. TROUBLESHOOTING

Machine issues

1. The main mask display is composed of a customized LCD panel with a protective glass, adhered by a special glue film. This glue film is provided along with the glass and can be glued manually, and even removed and re-attached as long as no dust particles get in the way.
If the mini build platform is leveled too low (too tight with respect to the glass), the centered force may cause some bubbles to appear on the periphery of the active area of the display. This case has a simple solution, by applying light pressure on the glass and sliding a finger from the center to the outside, the bubbles will disappear. And of course, re-level the mini build platform further away from the glass.
2. The build platform must be able to be firmly attached to the carriage. If you notice that the fit is not good, it may be necessary to make a small adjustment to the two carriage screws, so that the spherical head is centered in the magnet when tightening the hand knob screw.


## 10. TROUBLESHOOTING

Machine issues

3. The resin vat must be able to be placed on the magnets in such a way that the release film is completely in contact with the display glass. If this doesn't happen, you can loosen the screw on the magnet that you think is out of place, adjust the magnet, and retighten the screw.
4. Along with the machine accessories, three sets of washers are included, which are not initially necessary. If you think it is necessary, and as long as the release film of the resin vat is in contact with the display glass, you can add a set of washers (0.1, 0.2 or 0.3 mm) under the 4 magnets (between the magnets and the PCB). In this way, the magnets are brought closer to the vat frame, increasing their holding force.

## 11. MINI RESIN VAT & BUILD PLATFORM


1 piece
70 x 100 mm

1 piece
70 x 100 mm

Prior to installing the film in the mini resin vats, cut the films provided (100 x 140 mm) into 2 pieces of 70 x 100 mm. Beyond that, the procedure is similar to that of standard vat, according to section 7.

Remove the hand knob
screw and replace it
with the provided M3 x
10 screw. This screw
will allow you to adjust
and release the mini
build platform using
the 2mm allen key.
(The hand knob screw
collides with the mini
resin vat).

## 11. MINI RESIN VAT & BUILD PLATFORM

Place the magnetic adapter first.

Next, insert the mini resin vat from above and very slightly adjust the hand knob screw.

Leveling is done in the same way as the standard build platform, see section 4. The only thing that changes here is that a 2 mm Allen wrench is needed to loosen and tighten the M3x10 screw that replaces the hand knob tightening screw.

The mini vat is positioned as follows:

## 12. USER NOTES


RESIN →

1. LAYER HEIGHT (um) | 100

2. INITIAL EXPOSURE (s) | 40

3. EXPOSURE TIME (s) | 6.0

4. UV POWER | 255

5. BOTTOM LAYER COUNT | 5

6. TRANSITION LAYERS | 0

7. BOTTOM LIFT HEIGHT(mm) | 6.00

8. LIFT HEIGHT (mm) | 4.00

9. BOTTOM LIFT SPEED (mm/s) | 0.70

10. LIFT SPEED (mm/s) | 1.70

11. RETRACT SPEED (mm/s) | 2.90

12. REST TIME (ms) | 0

RESIN →

1. LAYER HEIGHT (um)
2. INITIAL EXPOSURE (s)
3. EXPOSURE TIME (s)
4. UV POWER
5. BOTTOM LAYER COUNT
6. TRANSITION LAYERS
7. BOTTOM LIFT HEIGHT(mm)
8. LIFT HEIGHT (mm)
9. BOTTOM LIFT SPEED (mm/s)
10. LIFT SPEED (mm/s)
11. RETRACT SPEED (mm/s)
12. REST TIME (ms)

## 12. USER NOTES

## 12. USER NOTES

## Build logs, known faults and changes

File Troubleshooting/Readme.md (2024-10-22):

**We will list here the issues found on the Crowd Supply campaign machines, and their solutions**

First of all, PLEASE READ THOROUGHLY:

1) [Quick start guide and slicer configuration](https://github.com/Lite3DP/Lite3DP-Gen-2/tree/main/Gen%202%20-%20Quick%20Start%20Guide)

2) [Crowd Supply updates](https://www.crowdsupply.com/lite3dp/lite3dp-gen-2/updates). Important information was included here that cannot be found elsewhere.

For those new to MSLA 3D printing, building knowledge will take some time. Be patient and enjoy the process, study and consult different online sources, there is a lot of information that does not make sense to replicate here. Trial and error will make you an expert.

The machines were rigorously tested before being shipped. However, we have heard of some alterations due to the long journey around the globe:

1) First of all, a damaged micro SD card can affect the startup and operation of the machine. Please make sure to start and test it without inserting any card.

2) If the touchscreen display does not display anything when you turn on the machine, or displays a blurry image, or does not respond to touch:

There is most likely **an exposed trace on the main board that is touching the black aluminum rectangular tube**, the one under the mask display. To check, please carefully remove the 2 M2 screws holding the linear guide to the rear aluminum plate of the cover (the bottom one and the top one, those who have the nuts). Then remove all 12 black M3 screws from the base of the machine. Disconnect the 4-wire cable that connects the main board to the base board. Be careful of the loose inner reflective cone. Look for scratched traces around the display, yellow area in the image below. If so, **simply place a piece of electrical tape over the exposed trace and reassemble.** (Before reassembling, please check that the flexible flat cable that connects the touch board to the main board is correctly positioned.) 



Example of what an exposed trace looks like:

370587735-61a19d3a-b51b-4551-bf8a-fbd302da99e3

3) Some thermoformed plastic covers may have contracted during manufacturing, causing them to scratch against the folded aluminum plate. Here you can simply remove the 4 M3 screws and turn the black POM wheels over, leaving the letters "L" and "R" facing the inside of the machine, like the following image (Please be careful when handling the cover. Excessive force may break it):



4) Manually stretching the silicone cover tightly, from the edges and in both directions, will help a better fit on the resin vat. (Repeat several times)



5) The carriage includes a concave magnet and ball system, allowing for convenient clamping, easy platform leveling and tightening with a single hand knob screw. This tightening is achieved through the action of 2 fixed screws and the hand knob screw. When tightening the latter, the 3 screws must be symmetrical in contact with the 10mm diameter spherical part of the platform. It is a system as simple as it is effective, achieving a perfectly firm hold, although for its proper functioning a correct position of the two fixed screws is necessary.
In the latest revisions to the Gen 2 design, and in order to facilitate the positioning of the two fixed screws, we decided to include two CNC machined nuts. However, due to small inaccuracies in the length of the screws or the placement of the threaded insert, there may be some cases where the screws do not reach the desired depth, even by adjustment. In these cases it is recommended to proceed as follows:

a) Raise the carriage to its maximum height, to facilitate the operation. (As always, be careful not to exceed the maximum height.)

b) Unscrew the two fixed screws and remove the two machined nuts.

c) Re-screw the two screws without the machined nuts (store them just in case).

d) To achieve the proper depth of the two fixed screws, insert the platform into the concave magnet. Screw (preferably manually for greater sensitivity) the two screws until you feel that there begins to be a slight resistance.

e) Check that the adjustment was correct by tightening the platform with the hand knob screw. A correct position of the screws will ensure that when tightening the hand knob screw the platform will be perfectly fixed, and will not move or rotate during tightening. (See reference image in section 10.2 of the quick start guide).

6) The application counts all files in the print folder, since depending on the Slicer and its version it may include some additional files like preview images, gcode, a readme file, etc. However, there was supposed to be a black screen before each image, so the last layers corresponding to these additional files that are not slice images are not printed at all. Evidently at some point this black screen was removed from the code without realizing it. The solutions to this problem are:
   
a) Remove the files that the Slicer generates that do not correspond to slice images from the print folder on the micro SD card.

b) Update the firmware to v1.1 or later.

7) For the "Touch pencil" test print and 0.025mm layer thickness, a missing line of code was found, which made the screen black before drawing the circular section in the last layers, printing the progress screen. It was corrected in firmware v1.1. (This did not affect other layer thicknesses or other test files or micro SD card files, which have their own printing function.)

**Some clarifications:**

1) All machines have been delivered with firmware v1.0 loaded.

2) Next to the power button, at the bottom of the main board, works the LDO voltage regulator, which can reach 90°C/200°F in normal operation.

3) In the menu, after selecting the micro SD card folder, you should be able to see a brief preview with the sections of the part/s to be printed. If not, check that the Slicer configuration is correct or that the micro SD card is in FAT32 format (and not damaged).

4) In all types of release films, we have experimentally observed that the peel forces are higher in recently installed films, so some precautions must be taken: select lower lifting speeds and if possible print smaller sections.

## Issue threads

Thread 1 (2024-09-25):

light tunnel above uv leds scratches pcb

chri2, 2024-09-25:
The anodized black tunnel between bottom pcb (uv leds) and mainboard and the metallic-silver light funnel inside it scratch the bottom and main pcb. The protective layer of varnish above the copper paths of the pcb can be scratched away when the printer is transported due to the vibrations of the movement.

In my case this resulted in the touchscreen not working or sometimes showing distorted pages.

To repair Alfredo wrote:

> It may be that there is an exposed track on the main board that is touching the black aluminum tube, the one under the mask display. To check, please carefully remove the 2 M2 screws holding the linear guide to the rear aluminum plate of the cover (the bottom one and the top one, which have the nut). Then remove all 12 black M3 screws from the base of the machine. Disconnect the 4-wire cable that connects the main board to the base board. Check that there are no exposed tracks around the display (it will look gold), at the bottom of the main board and around the mask display. If so, simply place a piece of electrical tape over the exposed track and reassemble.

Examples for broken menu pages:
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

Scratches on the main pcb leaving the paths blank:
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

Bottom pcb with paths covered where metal touches them:
**WARNING: the tape I used in the picture might not resist the heat emitted by the leds.**
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

Metal tube with edge covered with tape:
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

chri2, 2024-09-27:
Better idea than tape to insulate:

Print some thin layers based on the [dimension of the tube and cone](https://github.com/Lite3DP/Lite3DP-Gen-2/blob/main/Hardware/Plastic%20parts/Cone.STL) and some washers of the same thickness to put between tube and PCBs.

If I'll find time to do that, I'll publish the stl here.

Lite3DP, 2024-10-22:
Solution added to [Troubleshooting guide](https://github.com/Lite3DP/Lite3DP-Gen-2/tree/main/Troubleshooting).

Closed 2024-10-22.

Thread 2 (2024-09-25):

touchscreen went black on longer print

chri2, 2024-09-25:
When printing the _touchpen_ testprint the screen at some point went black, but the print went through with no errors.

Might be related to https://github.com/Lite3DP/Lite3DP-Gen-2/issues/1

Lite3DP, 2024-10-22:
Solution added to [Troubleshooting guide](https://github.com/Lite3DP/Lite3DP-Gen-2/tree/main/Troubleshooting).

Closed 2024-10-22.

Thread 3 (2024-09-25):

platform tilted during print

chri2, 2024-09-25:
Testprinting the keychain the platform tilted even though I already feared I'd fastened the screw to fix it to strong.

Disassambled the printer to reach the screw on the back of the head holding the paltform and took away the plastic washer and replaced it with a slightly thinner one. Did the same for the screw on the left front of the head.

Before changing the washers the two screws were just visible from inside the head holding the platform, but didn't stick into it.

I had the impression the space between magnet holding the platform and screws to fix it could be bigger so that the screws would grab a bit lower on the metal knob of the platform. This would help to hold the platform more secure.

If you'll need pictures - please let me know.

Lite3DP, 2024-10-22:
Solution added to [Troubleshooting guide](https://github.com/Lite3DP/Lite3DP-Gen-2/tree/main/Troubleshooting).

chri2, 2024-10-25:
There's been some questions about the platform not being hold strong enough in the head on the chat.

To get down to the root of the problem I looked very closely at my Lite3DP.

Here's a drawing the is supposed to show a cut through the head with the knob holding the platform inside it and the one thumb screw:

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

Closing the screw should fasten the knob inside the head.

I observed on my printer that the screw pushes the knob towards the edge of the magnet ring (ruled in the drawing) like shown by the red arrows:

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

The green line is supposed to show the surface the knob is pushed against. If the screw is fastened tight, it'll push the knob out of the magnet ring sliding over the green edge as shown here:

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

This is where the **two other screws** become important. They can deliver the support from two more sides to hold the knob in place.

**But this only works** if they are not too short so that the knob can be pushed out of the magnet ring by any other screw (letting it slide out of the head while gliding over the edge of the magnet as shown above) **and** if they are not to long to not let the knob settle completely inside the magnet ring.

What I did to adjust the three screws:

* screwed all three screws out as far as I could not see the end pointing inside the head anymore
* placed the platforms knob inside the head on the magnet ring (held by the magnet)
* while holding the platform slightly against the head
  * screwed in the screws each a bit going through all screws again and again **using no force at all**
  * while doing so taking care that the platform wouldn't slide any micrometer out of the magnet ring
* after all screws had been fastened **very, very slightly** without any force and the knob of the platform not moving out of the head a single micrometer
  * fastened the thumb screw moderately
  * fastened the other two screws moderately
  * went through all three of them again fastening them a bit more (but with much less force I'd use on the the thumb screw when preparing a print)
* opened the thumb screw all the way
* took the platform out

I believe at this point I had the correct position for the two other screws to hold the platform with maximum force if the thumb screw is closed and **without pushing the platforms knob out of the magnet ring** anymore.

Without moving the two screws (without the thumb wheel) again I applied locking paint on the inside and outside of the head hoping that it would crouch inside the screw thread a bit and fix the screws in place.

Testing afterwards revealed that the platform is fixed very tight inside the head. In my case this has been a big improvement, because even though I had tried to adjust the two other screws before I hadn't found the right position.

Since my first attempt the [troubleshooting guide](https://github.com/Lite3DP/Lite3DP-Gen-2/blob/main/Troubleshooting/Readme.md) has already been updated.

This is how my adjustment looked afterwards:

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

@Lite3DP if you want to use any of the drawings, photos or explanation please feel free to copy.

chri2, 2024-10-30:
Trying to print [this relief](https://github.com/Lite3DP/Lite3DP-Gen-2/issues/15#issuecomment-2442390235) lying flat on the platform I found that the platform - even I did all the above - still gradually tilted during the print and the prints came out like this:

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

On the left three ones you can see that a cross section would look like a parallelogram. This is because on all three prints the platform tilted:

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

To get more friction between the head and the platforms knob I coated the knob of the platform thinly with resin and cured that.

This is how I ended up with the nearly perfect fourth print on the right side:

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

When printing large objects flat on the platform this might be a hack to get the platform really secured.

On discord in #general @SPI84 wrote: "After few failures with whole plate prints I've switched plate screws to made from diffrent alloy and additionaly tapared them, finnaly succes" - so replacing the screws might be another option. Hopefully @SPI84 will add details here.

chri2, 2024-10-30:
> On discord in #general @SPI84 wrote: "After few failures with whole plate prints I've switched plate screws to made from diffrent alloy and additionaly tapared them, finnaly succes" - so replacing the screws might be another option. Hopefully @SPI84 will add details here.

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
_© SPI84 on 30.10.2024 on #general Discord channel for Lite3DP Gen2_

Closed 2024-10-22.

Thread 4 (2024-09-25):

platform got stuck moving up

chri2, 2024-09-25:
when doing the test print of the _keychain_ with the default parameters at some point the platform didn't move up further than some point and the printer made some mechanical noise. This repeated driving the platform up and down and when the print finished I had to carefully help the platform going up.

The print ended without the _Lite_ imprint on the keychain - obviously because the platform didn't loosen from the release film.

I tried again with slightly adjusted parameters:

Bottom lift height: 8.00 mm
Lift height: 6.00 mm
Lift speed: 1.30 mm/s

With those changes it worked.

andypiper, 2024-09-26:
what / where are the keychain and touchpen test prints you refer to in this issue and other issues?

Lite3DP, 2024-10-22:
Ensure proper platform adjustment and adequate lifting speed.

Closed 2024-10-22.

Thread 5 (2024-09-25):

The progression display is printed

neolao, 2024-09-25:
I tried to print the touchpen and the result is this:

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

You can see "99" and "TO FINISH".
I suppose that the image destined to the touch screen was used to print.
I can also say that the images (the sliced model + touch screen display) are merged.

chri2, 2024-09-25:
I had a similar issue: I selected a folder from the sdcard and briefly a yellow printed `Preview` appeared at the bottom of a otherwise black screen. Then the screen jumped to the `PARAMETERS` menu page.

I started the print and got something I think is the menu.
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

jene8774, 2024-09-26:
+1
It seems to be a bug that happens across the board, not an individual error.

chri2, 2024-09-29:
To check @jene8774 idea about the additional files which are not images of layers I started a print as generated by PrusaSlicer. The directory contains the following files:
```
$ ls -nl | head -n4; echo '[...]'; ls -nl | tail -n4
insgesamt 2336
-rw-r--r-- 1 1000 1000  419 29. Sep 13:31 config.ini
-rw-r--r-- 1 1000 1000 3004 29. Sep 13:31 prusaslicer.ini
-rw-r--r-- 1 1000 1000 2500 29. Sep 13:31 rmote300000.png
[...]
-rw-r--r-- 1 1000 1000  333 29. Sep 13:31 rmote300578.png
-rw-r--r-- 1 1000 1000  318 29. Sep 13:31 rmote300579.png
-rw-r--r-- 1 1000 1000  287 29. Sep 13:31 rmote300580.png
drwxr-xr-x 2 1000 1000 4096 29. Sep 13:32 thumbnail
```

So there are at least two files that are not layer images and maybe the subdirectory will be counted as an additional file also.

neolao, 2024-09-29:
Oh I see. I will try removing unnecessary files

chri2, 2024-09-30:
related to #8

Closed 2024-10-22.

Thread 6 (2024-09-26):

This point is to HOT.

jene8774, 2024-09-26:
This point is too hot.
is this correct or error?

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

chri2, 2024-09-29:
I asked that already when I had trouble getting my Lite3DP started and Alfredo replied:

> Don't worry about the 1117 voltage regulator, it works at about 200°F.

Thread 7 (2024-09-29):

Setting for Supports for PrusaSlicer in Quick Start Guide missing?

chri2, 2024-09-29:
https://github.com/Lite3DP/Lite3DP-Gen-2/blob/main/Gen%202%20-%20Quick%20Start%20Guide/Gen%202%20-%20slicer%20configuration.pdf

One of my first prints with supports didn't come out good, because the support beams weren't connected to the object.

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

Looking around in PrusaSlicer I found a setting for how thick the supports should be at there ending and increased that.

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

It became better. I'm just printing now another test with `Print Settings / Supports / Pinhead front diameter` set to 0.75mm to test whether this helps to improve.

Lite3DP, 2024-10-22:
Support features must be set according to the part to be printed and the resin used. There is no universal setting.

Closed 2024-10-22.

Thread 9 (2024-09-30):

silicon covers for vat are too small

chri2, 2024-09-30:
I can only make the top cover to stay on the vat with a lot of trying and pushing it back on.

[2024-09-30-130633.webm](https://github.com/user-attachments/assets/21945607-80e7-4c4a-9804-282022fd49cf)

Lite3DP, 2024-10-22:
Solution added to (Troubleshooting guide)[https://github.com/Lite3DP/Lite3DP-Gen-2/tree/main/Troubleshooting].

Closed 2024-10-22.

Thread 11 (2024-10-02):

printing parameters for different resins

chri2, 2024-10-02:
On a chat this information will get lost sometimes. On the long run there should be some place to store them. Until that has been found we can store them here.

chri2, 2024-10-02:
Anycubic Water-Wash Resin+

Layer Height: 50
Initial Expos.: 40
Exposure Time: 6.00
UV POWER: 255
Bottom Layers: 5
Trans. Laysers: 0
B. Lift Height: 8.0
Lift Height: 6.0
Lift Speed: 1.30
Retr. Speed: 2.90
B.Lift Speed: 0.70
Rest Time: 0

Probably not optimal, yet. Please comment.

chri2, 2024-10-22:
Anycubic Tough 2.0

Layer Height: 50
Initial Expos.: 25
Exposure Time: 6.00
UV POWER: 255
Bottom Layers: 5
Trans. Laysers: 0
B. Lift Height: 8.0
Lift Height: 5.0
Lift Speed: 0.50
Retr. Speed: 2.90
B.Lift Speed: 0.50
Rest Time: 0

Faster lift speed and lower exposure times resulted in supports not being printed.

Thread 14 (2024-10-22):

tools / clean resin vat - exposure not on whole screen

chri2, 2024-10-22:
I tried the function and here is a picture of what I had:

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

I would have expected that I'd get a square without holes

chri2, 2024-10-22:
Exposure time has been 45 seconds. Here are pictures of the UV running without vat and of the screen with lights off:

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

Lite3DP, 2024-10-22:
@chri2 Yes, please check that there is nothing under the display.
Also remember that both the mask display and the touchscreen show the same thing, just that due to the lack of backlight nothing is visible on the mask display. Carefully, with the machine disassembled (without cover or base), you can use a flashlight to illuminate the mask display while you navigate the menu and see better where those spots are coming from. In a very rare case, they may be dead areas on the display, hopefully this is not the case.

chri2, 2024-10-23:
O.k. I took the printer apart and took some pictures. I used some led lights to put lights to the back of the screen while taking the pictures.

## screen off

In these pictures the screen is off and the printer is not powered.

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

## screen active

I powered the printer and took these pictures.

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

The following pictures are taken while the clean vat tool has been active.

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

## screen inspection from the back

I carefully controlled the back of the screen for dirt or any signs that may explain the problem seen in the pictures above, but didn't find any. Looking at the silvery back of the screen in daylight the errors from the pictures above can barely be seen as shadows - nearly not notable. I think the visual effect is so weak I can't put it into a photo.

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

Please let me know if I can provide more information to help solve the problem.

Lite3DP, 2024-10-23:
Sorry @chri2 they look like two dead zones on the LCD. Could it be that the edge of the platform hit the display during leveling? I haven't seen anything like this before. It's not the best, but you can still use the machine preventing print sections from including dead zones. However, you might want to order a replacement LCD display from CS before they run out. Sorry again.

chri2, 2024-10-24:
> Sorry @chri2 they look like two dead zones on the LCD. Could it be that the edge of the platform hit the display during leveling?

No. And it doesn't look like cracks neither like hits.

> I haven't seen anything like this before. It's not the best, but you can still use the machine preventing print sections from including dead zones. However, you might want to order a replacement LCD display from CS before they run out. Sorry again.

Uhm, I'd say this is a production error. I do not see any way how one could inflict a damage like that - like you probably do neither. I'd expect that I'd get provided a screen as a replacement given that I'm able to change it (which probably is possible since there are screens to order).

I do not see where my fault should be in this that I'd have to pay for the replacement screen?

Lite3DP, 2024-10-24:
Customer support contact page: https://www.crowdsupply.com/contact

chri2, 2024-10-25:
Thanks for the suggestion! I did that and am waiting for their answer.

chri2, 2024-10-28:
@Lite3DP, could you provide some advice/guidance on how to remove the screen from the mainboard of the Lite3DP Gen2? Is it glued to the mainboard? Does heat help to free it?

chri2, 2024-10-29:
When I exchanged the screen I found that it is easily peeled off the pcb. It seems only to be held in place by adhesion.

Before removing the screen I opened the [THD THD0515-45CL-SN flat cable connector](https://www.lcsc.com/product-detail/FFC-FPC-Flat-Flexible-Connectors_THD-THD0515-45CL-SN_C283158.html) by carefully pulling up the flap of the [Front Flip-Lock Actuator](https://www.te.com/en/products/connectors/pcb-connectors/wire-to-board-connectors/ffc-fpc-ribbon-connectors/fpc-connectors/intro-to-fine-pitch-fpc-connectors.html) with my fingernail.

The new screen I carefully moved in its place maneuvering its flat cable into the **zero insertion force** (ZIF) connector that I opened to remove the old screen.

My new screen had on its back (silver side) *two* foils:
* one is large and has a corner to grab to peel it off which I did
* the other one (I guess it is supposed to stick on the bigger first one and get peeled off when pulling the thicker one off, but that didn't work for me) I very carefully lifted with a plastic card at one corner until I could grab it with my fingers.

The upper side (black) had a foil installed also.

My new screen works and has no broken areas.

Closed 2024-10-22.

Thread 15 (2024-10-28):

Problems printing objects that extend towards the edges of the screen

chri2, 2024-10-28:
I've tried printing planes, because I wanted to learn how to get a case for some PCB out of the printer. The case is much larger than the printer allows to print, so I cut it into pieces and tried different ways printing it. The parts that do not have overhangs are best printed flat on the platform.

The other parts didn't come out very well, yet. I always have problems towards the edges of the screen, like here:

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

For this object:
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

This has been printed in Anycubic Water-Wash Resin+ using the following parameters:

```
Layer Height: 50
Initial Expos.: 40
Exposure Time: 7.00
UV POWER: 255
Bottom Layers: 5
Trans. Laysers: 0
B. Lift Height: 8.0
Lift Height: 5.0
Lift Speed: 0.50
Retr. Speed: 2.90
B.Lift Speed: 0.20
Rest Time: 0
```

I'd think those are quite slow and conservative, but I'm a beginner. There are other errors in the print above than the edges for sure. The supports end before they bow over to the vertical plain I printed. So there **must be other factors to improve** than the one I'll look at now.

I was wondering what could be the differences between printing in the middle of the screen and towards the edges and came up with two possible factors:
* peel force is probably different towards the edge of the release film
* light distribution might be different

I tried to mitigate the difference in peel force using slow lifting speeds which improved the result, but didn't stop the problems toward the edges.

To look at the light distribution I put a camera on the head and took pictures of the screen:

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

I took a picture while running the _CLEANING RESIN VAT_ option. The picture is strongly under-exposured to offer a view towards the light source. The two faulty areas on the right edge are a problem with my screen that shouldn't have effected the print, because I avoided them when placing the object in the slicer:

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

The LEDs on the bottom of the tube can be clearly identified and there are some strong reflections from the mirror funnel.

I then put the vat on the printer filled with clear Water-Washable Resin+ and took another picture while running _CLEANING RESIN VAT_. This time the light has to filter trough the release film and the very low level of resin in the vat and the light distribution can be seen clearly:

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

The object I printed successfully and used to repair a remote control looks like this:

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

It is centered on the middle of the screen where the strongest light is emitted if my picture from above can be taken as some measure on how much light is emitted in which part of the screen.

## Conclusion

I don't know about the effects of over-exposure when printing SLA, but for the edges of the screen the only solution seems to be to increase the exposure time even more.

## Idea for improvement

It could be possible to compensate uneven light distribution **if this would make sense at all**:

* make a brightness map of the screen (e.g. by taking a picture)
* load the brightness map into the firmware
* calculate an exposure factor for each pixel depending on the amount of light in its area
* while printing one layer
  * start with all pixels for the png transparent
  * switch pixels in brighter areas to black after the given exposure time
  * leave pixels in darker areas of the screen longer transparent according to their calculated exposure factor

chri2, 2024-10-28:
To illustrate the issue with another example: I used the service  https://3dp.rocks/lithophane/ recommended by Alfredo Bonini to make a relief from this picture of a city wall in Campeche, México

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

and sliced it to be printed flat like this lying flat on the platform:

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

The result shows on the right between `D` and `C` edge the layers above the base layers (exposure 40 sec, same settings as above) missing. The missing piece below the `D` is the problem with my screen that has nothing to do with the suspected matter of the uneven exposure at the edges.

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

BTW: Thanks a lot for the hint to the page with the tool to convert pictures to reliefs! It is really great fun and I'm looking forward to learn how to do that in freecad!

chri2, 2024-10-30:
I replaced my broken screen to get rid of the little cut-out around the 'D' and tried using the following parameters:

```
Layer Height: 50
Initial Expos.: 30
Exposure Time: 20.00
UV POWER: 255
Bottom Layers: 5
Trans. Laysers: 0
B. Lift Height: 8.0
Lift Height: 5.0
Lift Speed: 0.20
Retr. Speed: 2.90
B.Lift Speed: 0.20
Rest Time: 0
```

The [platform tilted](https://github.com/Lite3DP/Lite3DP-Gen-2/issues/3#issuecomment-2446070672) during printing and after [solving](https://github.com/Lite3DP/Lite3DP-Gen-2/issues/3#issuecomment-2446070672) that the print came out quite well:

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

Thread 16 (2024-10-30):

Firmware upload instructions improvements

chri2, 2024-10-30:
Just went through the procedure - **thanks for documenting it so well!**

Here are some additions and corrections that might help to make it even better:

* Add "Please install ESP32 boards core version 2.0.17" from readme.md to the document and add instructions:
  * Add menu location for doing this (Arduino IDE V2.3.3): Tools / Board / Boards Manager
  * Fill _esp32_ into _Filter your search..._
  * In section for _esp32 by Espressif Systems_ use the drop-down list beside the _UPDATE_ or _INSTALL_ button to select Version _2.0.17_
  * hit the _INSTALL_ button
* Add information (URL) about where to get the [Arduino IDE](https://www.arduino.cc/en/software)
* Add menu location for choosing the right board (Arduino IDE V2.3.3): Tools / Board / esp32 / ESP32 Dev Module
* In point 6 add information about whether the printer is allowed to be connected to a 12V power supply while powering it from usb-c via the CP2102 board (I disconnected the main 12V power while flashing)
* In point 9 change _Hit Upload until the upload is complete._ into _Hit Upload and wait until the upload completed._ (the button does not need to be pressed all the time while uploading `*eg*` 😉)

chri2, 2024-10-30:
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

ajwatt, 2024-11-14:
I will add an additional clarification for point 7:

- Press and hold the BOOT button, then press and release the RST button, then release the BOOT button.

If you release both buttons at the same time, as the current wording suggests, the printer will simply reboot.

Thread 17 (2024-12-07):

only one directory on sdcard visible

chri2, 2024-12-07:
Some point at time after upgrading to firmware 1.1 I found that the selection for printing objects saved on sdcard does only show one of the entries on the sdcard.

I tried various different naming like `A_B`, `B`, `A`, `test`. If there are two directories on the sdcard I can only select one of them and the other does not show up in the menu of the printer.

I took care to copy all the files before inserting the sdcard into the printer and then switching it on.

I formated a second (different) sdcard, tried that and it didn't change anything.

Lite3DP, 2024-12-07:
It's not a problem with v1.1. Please check with another micro SD card, format it, etc.

Closed 2024-12-07.

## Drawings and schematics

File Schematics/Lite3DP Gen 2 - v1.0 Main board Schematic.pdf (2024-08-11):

# VINBACKLIGHT

# +3.3V MS¹ MS² MS³

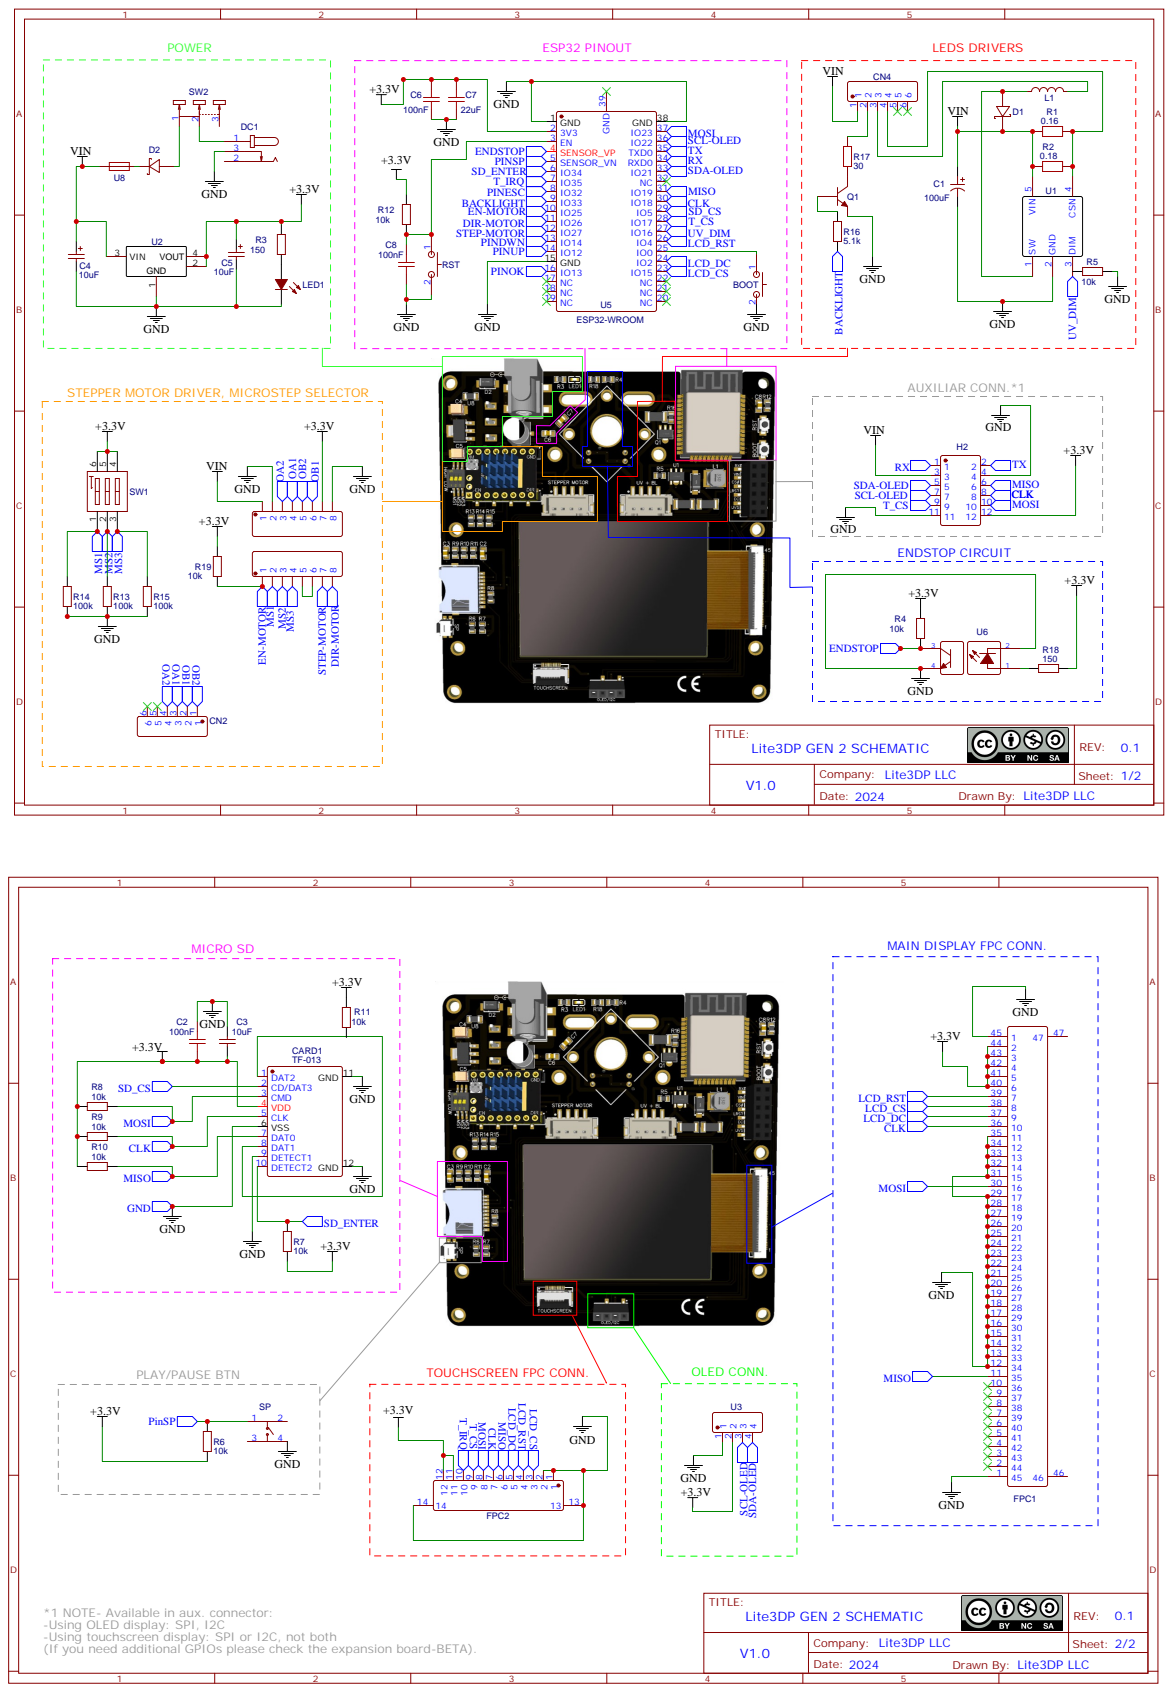
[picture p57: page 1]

MAIN DISPLAY FPC CONN.

*1 NOTE- Available in aux. connector:
-Using OLED display: SPI, I2C
-Using touchscreen display: SPI or I2C, not both
(If you need additional GPIOs please check the expansion board-BETA).

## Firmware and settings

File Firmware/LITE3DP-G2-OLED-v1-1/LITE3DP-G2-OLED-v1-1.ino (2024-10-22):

////////////////////////////////////////////////////////////

/*
  Lite3DP Gen 2 v1.1 - OLED auxiliary display

  https://github.com/Lite3DP/Lite3DP-Gen-2

  MIT License

  Please visit www.lite3dp.com for more information, documentation and software.

  email: support@lite3dp.com

*/

////////////////////////////////////////////////////////////

/*
  LIBRARIES USED:

  Thank you very much to the following libraries creators!

  1) TFT_eSPI by Bodmer
     https://github.com/Bodmer/TFT_eSPI

  2) SDFat by Greiman
     https://github.com/greiman/SdFat

  3) PNGdec by bitbank2
     https://github.com/bitbank2/PNGdec

  4) Adafruit_SH110X by Adafruit
     https://github.com/adafruit/Adafruit_SH110x

  5) Adafruit_GFX by Adafruit
     https://github.com/adafruit/Adafruit-GFX-Library

  6) Adafruit_BusIO by Adafruit
     https://github.com/adafruit/Adafruit_BusIO

  7) Converter tool, file to C style array converter by notisrac
     https://notisrac.github.io/FileToCArray/
     https://github.com/notisrac/FileToCArray

*/

////////////////////////////////////////////////////////////

/*
  FIRMWARE UPLOAD:

  1) Install ESP32 board core 2.0.17 in Arduino IDE. Here is a good tutorial: https://randomnerdtutorials.com/installing-the-esp32-board-in-arduino-ide-windows-instructions/

  2) Install the 6 libraries. If you already have a library with the same name installed, delete it or temporarily move it from the libraries folder.

  2) Select Board: ESP32 Dev Module

  3) Connect the main board with the USB-C auxiliary board. Please be careful, an incorrect position could damage the main board.

  4) On the Gen 2 main board, press the RST button, and without releasing it, press the BOOT button. Release RST and then release BOOT.

  5) Upload firmware and reset.

*/

////////////////////////////////////////////////////////////

// **** PARAMETERS ****

float hLayer;              // Layer height (mm)

float hUp;                   // Lift height (mm)

float hUpInitial;            // Inital layers lift height (mm)

int FirstLayers;           //Number of bottom layers

int TraLayers;       //Number of transition layers

float expotime;            //Exposure time (s)

int iexpotime;             //Bottom exposure time (s)

float LiftSpeed;             // Lift speed (mm/s)

float LiftSpeedInit;         // Bottom lift speed (mm/s)

float RetractSpeed;          // Retract speed (mm/s)

int RestTime;             // Delay after retract (ms)

int PWMUV;                 // UV power (0-255)

int PWMBL = 255;                 // White backlight brightness (0-255)


int Lguide = 115;           //Total length of linear guide

float pitch = 2.44;              //Pitch of movement screw thread

int stepsMotorPerRev = 200;     //Motor steps per revolution (including gear reduction, if any)

int microsteps = 64;       //Driver microsteps

////////////////////////////////////////////////////////////

// Pin definition

#define PinDir 26
#define PinStep 27
#define PinEn 25

//#define sclk 18
//#define miso 19
//#define mosi 23
//#define cs   15
//#define dc   2
//#define rst  4

#define SDcs 5

#define BtnUp 12
#define BtnDown 14
#define BtnNext 13
#define BtnBack 32

#define PinEndStop 36

#define LightPin 16
const int freq = 5000;
const int ledChannel = 0;
const int resolution = 8;

#define BacklightPin 33
const int freq1 = 5000;
const int ledChannel1 = 1;
const int resolution1 = 8;

#define SdEnter 34

#define BtnPlay 39



#include "OLED-templates.h"
#include "OLED-test-print.h"
#include "keychain.h"
#include "menus.h"
#include "template12234.h"
#include "templatesDG.h"

///////////////////////////////////////////////

// ****LIBRARIES****

#include <Wire.h>
#include <Adafruit_GFX.h>
#include <Adafruit_SH110X.h>
#include <Fonts/FreeSans9pt7b.h>
Adafruit_SH1107 display = Adafruit_SH1107(64, 128, &Wire, -1, 400000, 100000);

#include <SPI.h>

#include <PNGdec.h>
#include <SdFat.h>
SdFat SD;

#include <Preferences.h>
Preferences preferences;

#include "SPI.h"
#include <TFT_eSPI.h>              // Hardware-specific library
TFT_eSPI tft = TFT_eSPI();

PNG png;

int16_t xpos = 0;
int16_t ypos = 27;

///////////////////////////////////////////////

// ****GLOBAL VARIABLES****

// **Screen number**

int screen = 0;


//**Button/SD status**

int edoBtnUP;
int edoBtnDOWN;
int edoBtnNEXT;
int edoBtnBACK;
int edoBtnPLAY;
int edoSdEnter;

//**Button delay**

#define delaybutton 100


//**Preview number of sections**

const int lenpreview = 30;

// **EndStop Lecture**

bool LectEndStop;


// **Layer Height**

int hLayerx1000 = hLayer * 1000;


// **Ascendant movement Height (mm)**

int maxheight = Lguide - 35;


// **Retract movement during printing**

float hDown;

float hDownInitial;


// **Steps per mm**

int StepsPerMm = stepsMotorPerRev * microsteps / pitch;


// **Calibration aditional steps**

const int maxAddDesc = 3;     // Additional maximum descent (Default = 3 mm)

long maxAddSteps = maxAddDesc * StepsPerMm / 80;

long stepsadditional;

int stepsadditionalx80 = 0;


// **Speed and time calculations**

int topdelay = 200;  // Movement delay between lift and retract

int delayLiftSpeed;

int delayLiftSpeedInit;

int delayRetractSpeed;

float updowntime;          //Light-off delay in seconds. Counted from turning off the UV light on one layer and turning on the UV light on the next one.

float updowntimeInit;      //For the initial layers.

long int updowntimeM;

// **For the correct name of file**

String DirAndFile;

String FileName;

int number;

String slicermode;
int slicernumber;


//**For the layers counter**

int LayersCounter = 0;

int Layers;

String dirfoldersel;


// **For the folder name**

File root;
File myfile;

char foldersel[25];

int counter = 1;


// **Progress**

int AdvLay = 0;
int xx0 = 32;
int yy0 = 40;
int xx1;
int yy1;
int alfaDegTot = 0;
float alfaRad;
int radius = 30;

unsigned long compTimeMillis = 0;

// **Test prints**

int PrintMode; // 0:micro SD File, 1:Keychain test, 2:OLED cover test


// Clean resin vat

int cleanexp = 45;


//Preferences modes: 0-Current, 1-Memory A, 2-Memory B, 3-Memory C, 4-Memory D, 5-Memory E, 6-Memory F

int PrefMode = 0;

//Select preferences from: 0-Menu preferences, 1-Menu print

int SelPrefMode = 0;
///////////////////////////////////////////////



void setup(void) {

  ReadPref();
  recalcTime();

  //UV Light, PWM
  ledcSetup(ledChannel, freq, resolution);
  ledcAttachPin(LightPin, ledChannel);
  ledcWrite(ledChannel, 0);

  //White backlight, PWM
  ledcSetup(ledChannel1, freq1, resolution1);
  ledcAttachPin(BacklightPin, ledChannel1);
  ledcWrite(ledChannel1, 0);

  pinMode (PinDir, OUTPUT);
  pinMode (PinStep, OUTPUT);
  pinMode (PinEn, OUTPUT);
  pinMode (PinEndStop, INPUT);
  pinMode (SdEnter, INPUT_PULLUP);

  pinMode (BtnPlay, INPUT);

  digitalWrite (PinEn, HIGH);
  tft.begin();

  tft.setRotation(3);
  coordRot3();

  displaymenuintro();

  //  delay(1200);

  screen = 0;
  displaymenuprint();

  OLEDintro();


}

////////////////////////////////////////////////////

void loop() {

  edoBtnUP = touchRead (BtnUp);
  edoBtnDOWN = touchRead (BtnDown);
  edoBtnNEXT = touchRead (BtnNext);
  edoBtnBACK = touchRead (BtnBack);
  edoBtnPLAY = digitalRead (BtnPlay);


  if (edoBtnPLAY == LOW) {
    btnPLAYmenu();
  }

  if (edoBtnUP < 20) {
    btnUPmenu();
  }

  if (edoBtnDOWN < 20) {
    btnDOWNmenu();
  }

  if (edoBtnNEXT < 20) {
    btnNEXTmenu();
    delaybtn();
  }

  if (edoBtnBACK < 20) {
    btnBACKmenu();
    delaybtn();
  }

}


////////////////////////////////////////////////////////////

//*** MENU FUNCTIONS ****

void btnUPmenu() {

  switch (screen) {

    case 1:
      displaymenuprint();
      screen = 0;
      break;

    case 11:
      folderUp(root);
      delaybtn();
      break;

    case 141:
      screen = 14;
      screen14B();
      delaybtn();
      break;

    case 142:
      screen = 141;
      screen141();
      delaybtn();
      break;

    case 143:
      screen = 142;
      screen142();
      delaybtn();
      break;

    case 144:
      screen = 143;
      screen143();
      delaybtn();
      break;

    case 145:
      screen = 144;
      screen144();
      delaybtn();
      break;

    case 146:
      screen = 145;
      screen145();
      delaybtn();
      break;

    case 147:
      screen = 146;
      screen146();
      delaybtn();
      break;

    case 2:
      displaymenusettings();
      screen = 1;
      break;


    case 21:                                   //screen 21 is when the platform is down during calibration
      if (stepsadditional > 0) {
        stepsadditional--;
        digitalWrite(PinDir, HIGH);
        digitalWrite (PinEn, LOW);
        for (int z = 0; z < 80; z++) {
          digitalWrite(PinStep, HIGH);
          digitalWrite(PinStep, LOW);
          delayMicroseconds(150);
        }
        digitalWrite (PinEn, HIGH);
      }
      break;

    case 2010:
      if (cleanexp < 360) {
        cleanexp++;
        tft.fillRect(120, 128, 240, 45, TFT_BLACK);
        tft.setTextColor(TFT_WHITE);
        drawCentreVariableInt(240, 150, cleanexp);
      }
      delaybtn();
      break;


    case 202:
      screen = 201;
      screen201B();
      delaybtn();
      break;

    case 32:
      screen = 31;
      screen31B();
      delaybtn();
      break;

    case 42:
      screen = 41;
      screen41B();
      delaybtn();
      break;

    case 52:
      screen = 51;
      screen51B();
      delaybtn();
      break;


    case 10011:
      switch (hLayerx1000) {
        case 25:
          hLayer = 0.05;
          hLayerx1000 = hLayer * 1000;
          tft.fillRect(120, 128, 240, 45, TFT_BLACK);
          drawCentreVariableInt(220, 150, hLayerx1000);
          tft.drawCentreString("um", 270, 150, 4);
          adjuststeps();
          break;

        case 50:
          hLayer = 0.1;
          hLayerx1000 = hLayer * 1000;
          tft.fillRect(120, 128, 240, 45, TFT_BLACK);
          drawCentreVariableInt(220, 150, hLayerx1000);
          tft.drawCentreString("um", 270, 150, 4);
          adjuststeps();
          break;

      }
      delaybtn();
      break;


    case 10012:
      if (iexpotime >= 1) {
        iexpotime++;
        tft.fillRect(120, 128, 240, 45, TFT_BLACK);
        tft.setTextColor(TFT_WHITE);
        drawCentreVariableInt(235, 150, iexpotime);
        tft.drawCentreString("s", 280, 150, 4);
      }
      delaybtn();
      break;


    case 10013:
      if (expotime >= 0.2) {
        expotime = expotime + 0.2;
        tft.fillRect(120, 128, 240, 45, TFT_BLACK);
        tft.setTextColor(TFT_WHITE);
        if (expotime <= 9.8) {
          tft.fillRect(120, 128, 240, 45, TFT_BLACK);
          drawVariableFloat(207, 150, expotime);
        }
        else if (expotime > 99.8) {
          drawVariableFloat3(200, 150, expotime);
        }
        else {
          drawVariableFloat2(200, 150, expotime);
        }

        tft.drawCentreString("s", 280, 150, 4);
      }
      delaybtn();
      break;


    case 10014:
      if (PWMUV < 255) {
        PWMUV++;
        tft.fillRect(120, 128, 240, 45, TFT_BLACK);
        tft.setTextColor(TFT_WHITE);
        drawCentreVariableInt(240, 150, PWMUV);
      }
      delaybtn();
      break;


    case 10015:
      if (FirstLayers < 20) {
        FirstLayers++;
        tft.fillRect(120, 128, 240, 45, TFT_BLACK);
        tft.setTextColor(TFT_WHITE);
        drawCentreVariableInt(240, 150, FirstLayers);
      }
      delaybtn();
      break;


    case 10016:
      if (TraLayers < 11) {
        TraLayers++;
        tft.fillRect(120, 128, 240, 45, TFT_BLACK);
        drawCentreVariableInt(240, 150, TraLayers);
      }
      delaybtn();
      break;


    case 10017:
      if (hUpInitial < 14.9) {
        hUpInitial = hUpInitial + 0.1;
        tft.fillRect(120, 128, 240, 45, TFT_BLACK);
        tft.setTextColor(TFT_WHITE);
        drawCentreVariableFloat(240, 150, hUpInitial);
      }
      delaybtn();
      break;


    case 10018:
      if (hUp < 15) {
        hUp = hUp + 0.1;
        tft.fillRect(120, 128, 240, 45, TFT_BLACK);
        tft.setTextColor(TFT_WHITE);
        drawCentreVariableFloat(240, 150, hUp);
      }
      delaybtn();
      break;


    case 10019:
      if (LiftSpeedInit < 8.1) {
        LiftSpeedInit = LiftSpeedInit + 0.1;
        tft.fillRect(120, 128, 240, 45, TFT_BLACK);
        tft.setTextColor(TFT_WHITE);
        drawCentreVariableFloat(240, 150, LiftSpeedInit);
        recalcTime();
      }
      delaybtn();
      break;


    case 10020:
      if (LiftSpeed < 8.1) {
        LiftSpeed = LiftSpeed + 0.1;
        tft.fillRect(120, 128, 240, 45, TFT_BLACK);
        tft.setTextColor(TFT_WHITE);
        drawCentreVariableFloat(240, 150, LiftSpeed);
        recalcTime();
      }
      delaybtn();
      break;


    case 10021:
      if (RetractSpeed < 8) {
        RetractSpeed = RetractSpeed + 0.1;
        tft.fillRect(120, 128, 240, 45, TFT_BLACK);
        tft.setTextColor(TFT_WHITE);
        drawCentreVariableFloat(240, 150, RetractSpeed);
        recalcTime();
      }
      delaybtn();
      break;


    case 10022:
      if (RestTime < 30000) {
        RestTime = RestTime + 100;
        tft.fillRect(120, 128, 240, 45, TFT_BLACK);
        tft.setTextColor(TFT_WHITE);
        drawCentreVariableInt(240, 150, RestTime);
      }
      delaybtn();
      break;

    case 100231:
      screen = 10023;
      screen10023B();
      delaybtn();
      break;

    case 100232:
      screen = 100231;
      screen100231();
      delaybtn();
      break;

    case 100233:
      screen = 100232;
      screen100232();
      delaybtn();
      break;

    case 100234:
      screen = 100233;
      screen100233();
      delaybtn();
      break;

    case 100235:
      screen = 100234;
      screen100234();
      delaybtn();
      break;

    case 100236:
      screen = 100235;
      screen100235();
      delaybtn();
      break;

  }
}

void btnDOWNmenu() {

  switch (screen) {

    case 0:
      displaymenusettings();
      screen = 1;
      break;

    case 1:
      displaymenuutilities();
      screen = 2;
      break;

    case 11:
      folderDown(root);
      delaybtn();
      break;

    case 14:
      screen = 141;
      screen141();
      delaybtn();
      break;

    case 141:
      screen = 142;
      screen142();
      delaybtn();
      break;

    case 142:
      screen = 143;
      screen143();
      delaybtn();
      break;

    case 143:
      screen = 144;
      screen144();
      delaybtn();
      break;

    case 144:
      screen = 145;
      screen145();
      delaybtn();
      break;

    case 145:
      screen = 146;
      screen146();
      delaybtn();
      break;

    case 146:
      screen = 147;
      screen147();
      delaybtn();
      break;

    case 21:                                   //screen 21 is when the platform is down during calibration
      if (stepsadditional <= maxAddSteps) {
        stepsadditional++;
        digitalWrite(PinDir, LOW);
        digitalWrite (PinEn, LOW);
        for (int z = 0; z < 80; z++) {
          digitalWrite(PinStep, HIGH);
          digitalWrite(PinStep, LOW);
          delayMicroseconds(150);
        }
        digitalWrite (PinEn, HIGH);
      }
      break;

    case 201:
      screen = 202;
      screen202();
      delaybtn();
      break;


    case 2010:
      if (cleanexp > 1) {
        cleanexp--;
        tft.fillRect(120, 128, 240, 45, TFT_BLACK);
        tft.setTextColor(TFT_WHITE);
        drawCentreVariableInt(240, 150, cleanexp);
      }
      delay(80);
      break;


    case 31:
      screen = 32;
      screen32();
      delaybtn();
      break;

    case 41:
      screen = 42;
      screen42();
      delaybtn();
      break;

    case 51:
      screen = 52;
      screen52();
      delaybtn();
      break;


    case 10011:
      switch (hLayerx1000) {
        case 50:
          hLayer = 0.025;
          hLayerx1000 = hLayer * 1000;
          tft.fillRect(120, 128, 240, 45, TFT_BLACK);
          drawCentreVariableInt(220, 150, hLayerx1000);
          tft.drawCentreString("um", 270, 150, 4);
          adjuststeps();
          break;

        case 100:
          hLayer = 0.05;
          hLayerx1000 = hLayer * 1000;
          tft.fillRect(120, 128, 240, 45, TFT_BLACK);
          drawCentreVariableInt(220, 150, hLayerx1000);
          tft.drawCentreString("um", 270, 150, 4);
          adjuststeps();
          break;
      }
      delaybtn();
      break;


    case 10012:
      if (iexpotime > 1) {
        iexpotime--;
        tft.fillRect(120, 128, 240, 45, TFT_BLACK);
        tft.setTextColor(TFT_WHITE);
        drawCentreVariableInt(235, 150, iexpotime);
        tft.drawCentreString("s", 280, 150, 4);
      }
      delaybtn();
      break;


    case 10013:
      if (expotime > 0.4) {
        expotime = expotime - 0.2;
        tft.fillRect(120, 128, 240, 45, TFT_BLACK);
        tft.setTextColor(TFT_WHITE);
        if (expotime <= 9.8) {
          tft.fillRect(120, 128, 240, 45, TFT_BLACK);
          drawVariableFloat(207, 150, expotime);
        }
        else if (expotime > 99.8) {
          drawVariableFloat3(200, 150, expotime);
        }
        else {
          drawVariableFloat2(200, 150, expotime);
        }
        tft.drawCentreString("s", 280, 150, 4);
      }
      delaybtn();
      break;


    case 10014:
      if (PWMUV > 0) {
        PWMUV--;
        tft.fillRect(120, 128, 240, 45, TFT_BLACK);
        tft.setTextColor(TFT_WHITE);
        drawCentreVariableInt(240, 150, PWMUV);
      }
      delaybtn();
      break;


    case 10015:
      if (FirstLayers > 1) {
        FirstLayers--;
        tft.fillRect(120, 128, 240, 45, TFT_BLACK);
        tft.setTextColor(TFT_WHITE);
        drawCentreVariableInt(240, 150, FirstLayers);
        recalcTime();
      }
      delaybtn();
      break;


    case 10016:
      if (TraLayers > 0) {
        TraLayers--;
        tft.fillRect(120, 128, 240, 45, TFT_BLACK);
        drawCentreVariableInt(240, 150, TraLayers);
      }
      delaybtn();
      break;


    case 10017:
      if (hUpInitial > 0.6) {
        hUpInitial = hUpInitial - 0.1;
        tft.fillRect(120, 128, 240, 45, TFT_BLACK);
        tft.setTextColor(TFT_WHITE);
        drawCentreVariableFloat(240, 150, hUpInitial);
        recalcTime();
      }
      delaybtn();
      break;


    case 10018:
      if (hUp > 0.6) {
        hUp = hUp - 0.1;
        tft.fillRect(120, 128, 240, 45, TFT_BLACK);
        tft.setTextColor(TFT_WHITE);
        drawCentreVariableFloat(240, 150, hUp);
        recalcTime();
      }
      delaybtn();
      break;


    case 10019:
      if (LiftSpeedInit > 0.1) {
        LiftSpeedInit = LiftSpeedInit - 0.1;
        tft.fillRect(120, 128, 240, 45, TFT_BLACK);
        tft.setTextColor(TFT_WHITE);
        drawCentreVariableFloat(240, 150, LiftSpeedInit);
        recalcTime();
      }
      delaybtn();
      break;


    case 10020:
      if (LiftSpeed > 0.1) {
        LiftSpeed = LiftSpeed - 0.1;
        tft.fillRect(120, 128, 240, 45, TFT_BLACK);
        tft.setTextColor(TFT_WHITE);
        drawCentreVariableFloat(240, 150, LiftSpeed);
        recalcTime();
      }
      delaybtn();
      break;


    case 10021:
      if (RetractSpeed > 0.2) {
        RetractSpeed = RetractSpeed - 0.1;
        tft.fillRect(120, 128, 240, 45, TFT_BLACK);
        tft.setTextColor(TFT_WHITE);
        drawCentreVariableFloat(240, 150, RetractSpeed);
        recalcTime();
      }
      delaybtn();
      break;


    case 10022:
      if (RestTime >= 100) {
        RestTime = RestTime - 100;
        tft.fillRect(120, 128, 240, 45, TFT_BLACK);
        tft.setTextColor(TFT_WHITE);
        drawCentreVariableInt(240, 150, RestTime);
        recalcTime();
      }
      delaybtn();
      break;

    case 10023:
      screen = 100231;
      screen100231();
      delaybtn();
      break;

    case 100231:
      screen = 100232;
      screen100232();
      delaybtn();
      break;

    case 100232:
      screen = 100233;
      screen100233();
      delaybtn();
      break;

    case 100233:
      screen = 100234;
      screen100234();
      delaybtn();
      break;

    case 100234:
      screen = 100235;
      screen100235();
      delaybtn();
      break;

    case 100235:
      screen = 100236;
      screen100236();
      delaybtn();
      break;

  }
}
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
